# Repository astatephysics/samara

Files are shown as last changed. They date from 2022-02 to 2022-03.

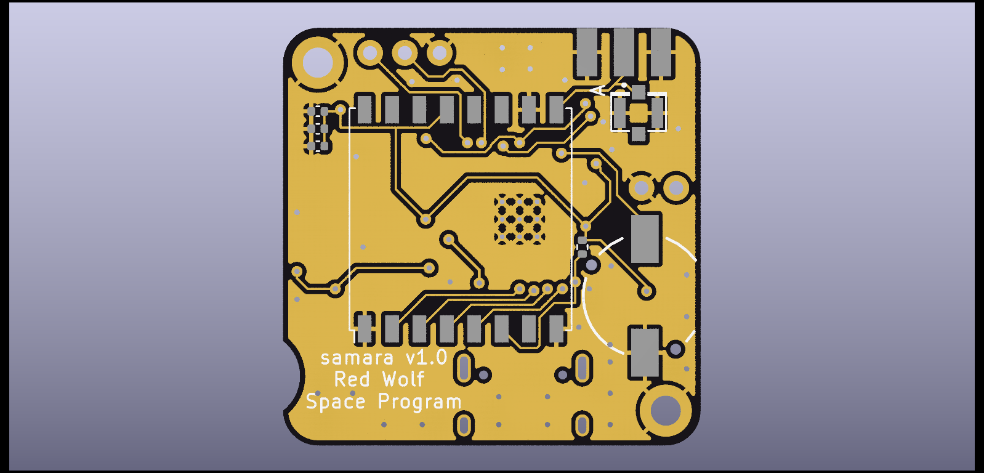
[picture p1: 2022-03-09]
samara-render-back.png

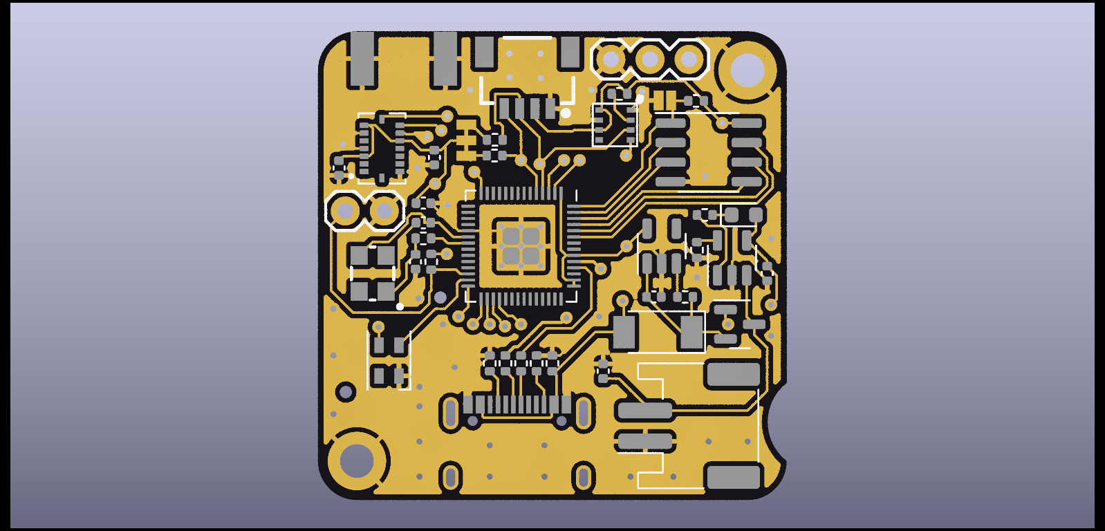
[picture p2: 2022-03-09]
samara-render-front.png

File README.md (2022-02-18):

# samara
Red Wolf Space Program's samara-style glider payload

----------------------------------------------------------
## Overview

Samara are a fruit with a fibrous wing-like structure that increases their wind-borne dispersal distances. Some of these like maple and ash seeds may slow their descent by autorotation as such they provide much entertainment for us humans who find them about. This project seeks to develop an airborne payload that mimic this behavior with a 3d printed airframe housing a radio antenna and this printed circuit board. 

This version of the board is contstrained to a 30.5mm x 30.5mm board and is inspired by "CricketSATs." This consists of a RP2040 microcontroller, BME280 temperature/humidity/pressure sensor, BNO055 inertial measurement unit, and RF95 LoRA radio. Several indicator leds are included as well as a surface mounted piezo buzzer. A STEMMA/Qwiic-compatable JST connector provides access to peripheral boards over I2C (e.g., GPS breakout board, realtime clocks, science payloads.)

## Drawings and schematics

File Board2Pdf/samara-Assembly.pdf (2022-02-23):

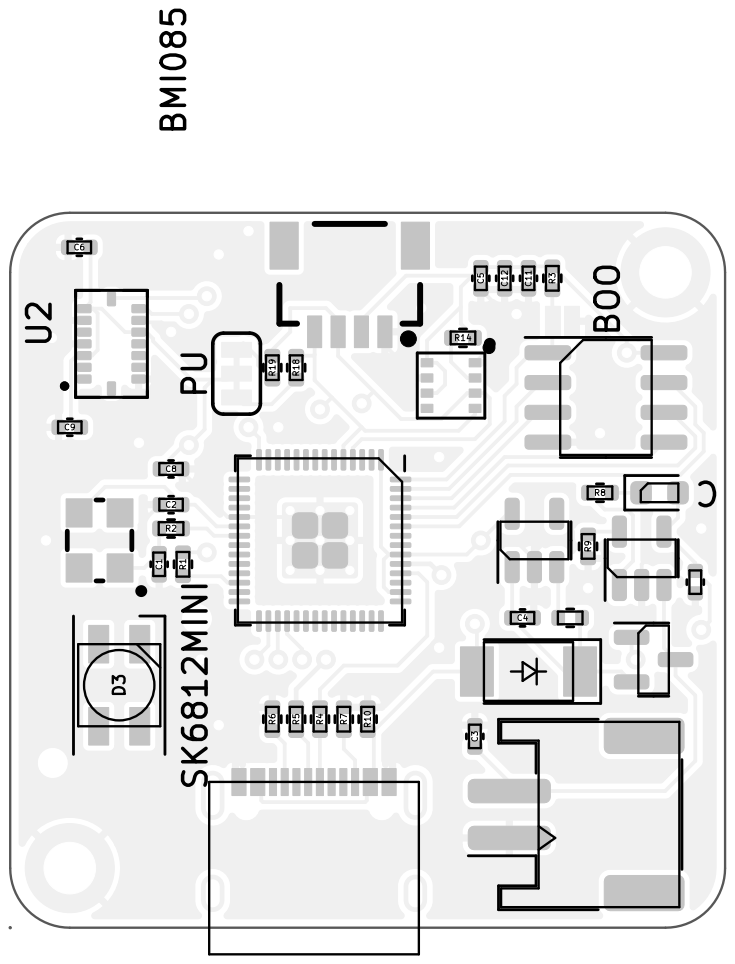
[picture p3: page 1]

Sheet: Assembly
File: samara.kicad_pcb
Id: 1/1 Title: samara payload prototype

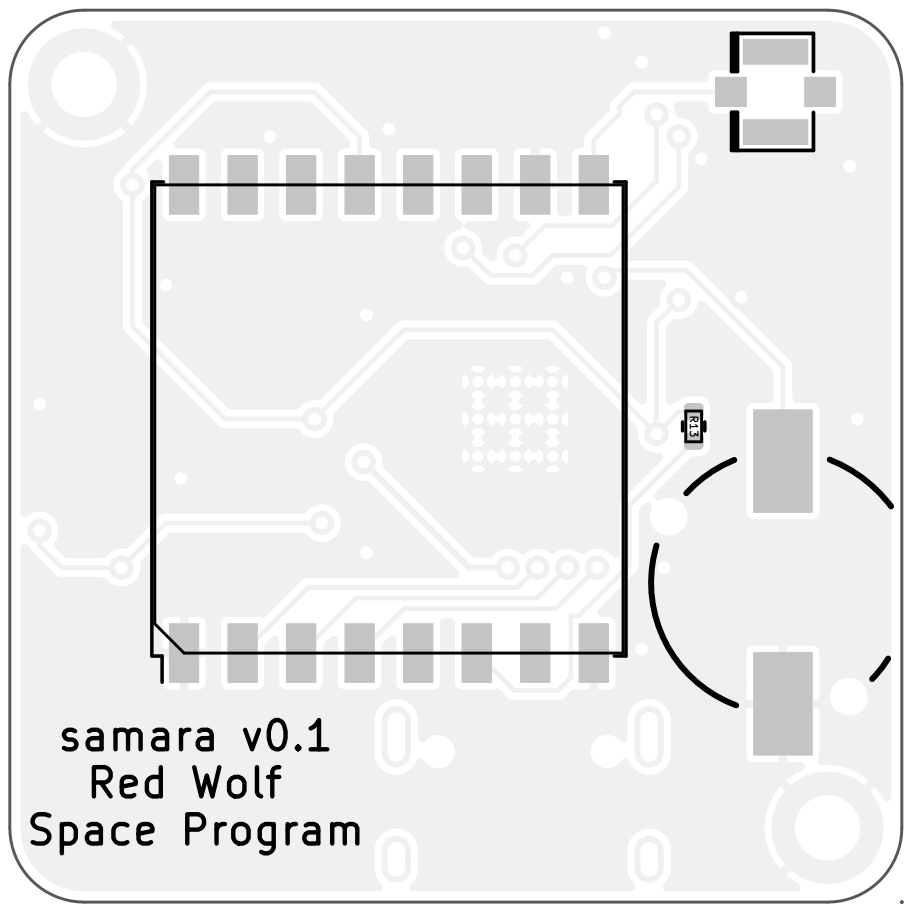
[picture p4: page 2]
D Date: KiCad E.D.A. kicad (6.0.1) Size: USLetter; Rev:

Arkansas State University R13

samara v0.1 Red Wolf Space Program

Sheet: Assembly
File: samara.kicad_pcb
Id: 1/1 Title: samara payload prototype

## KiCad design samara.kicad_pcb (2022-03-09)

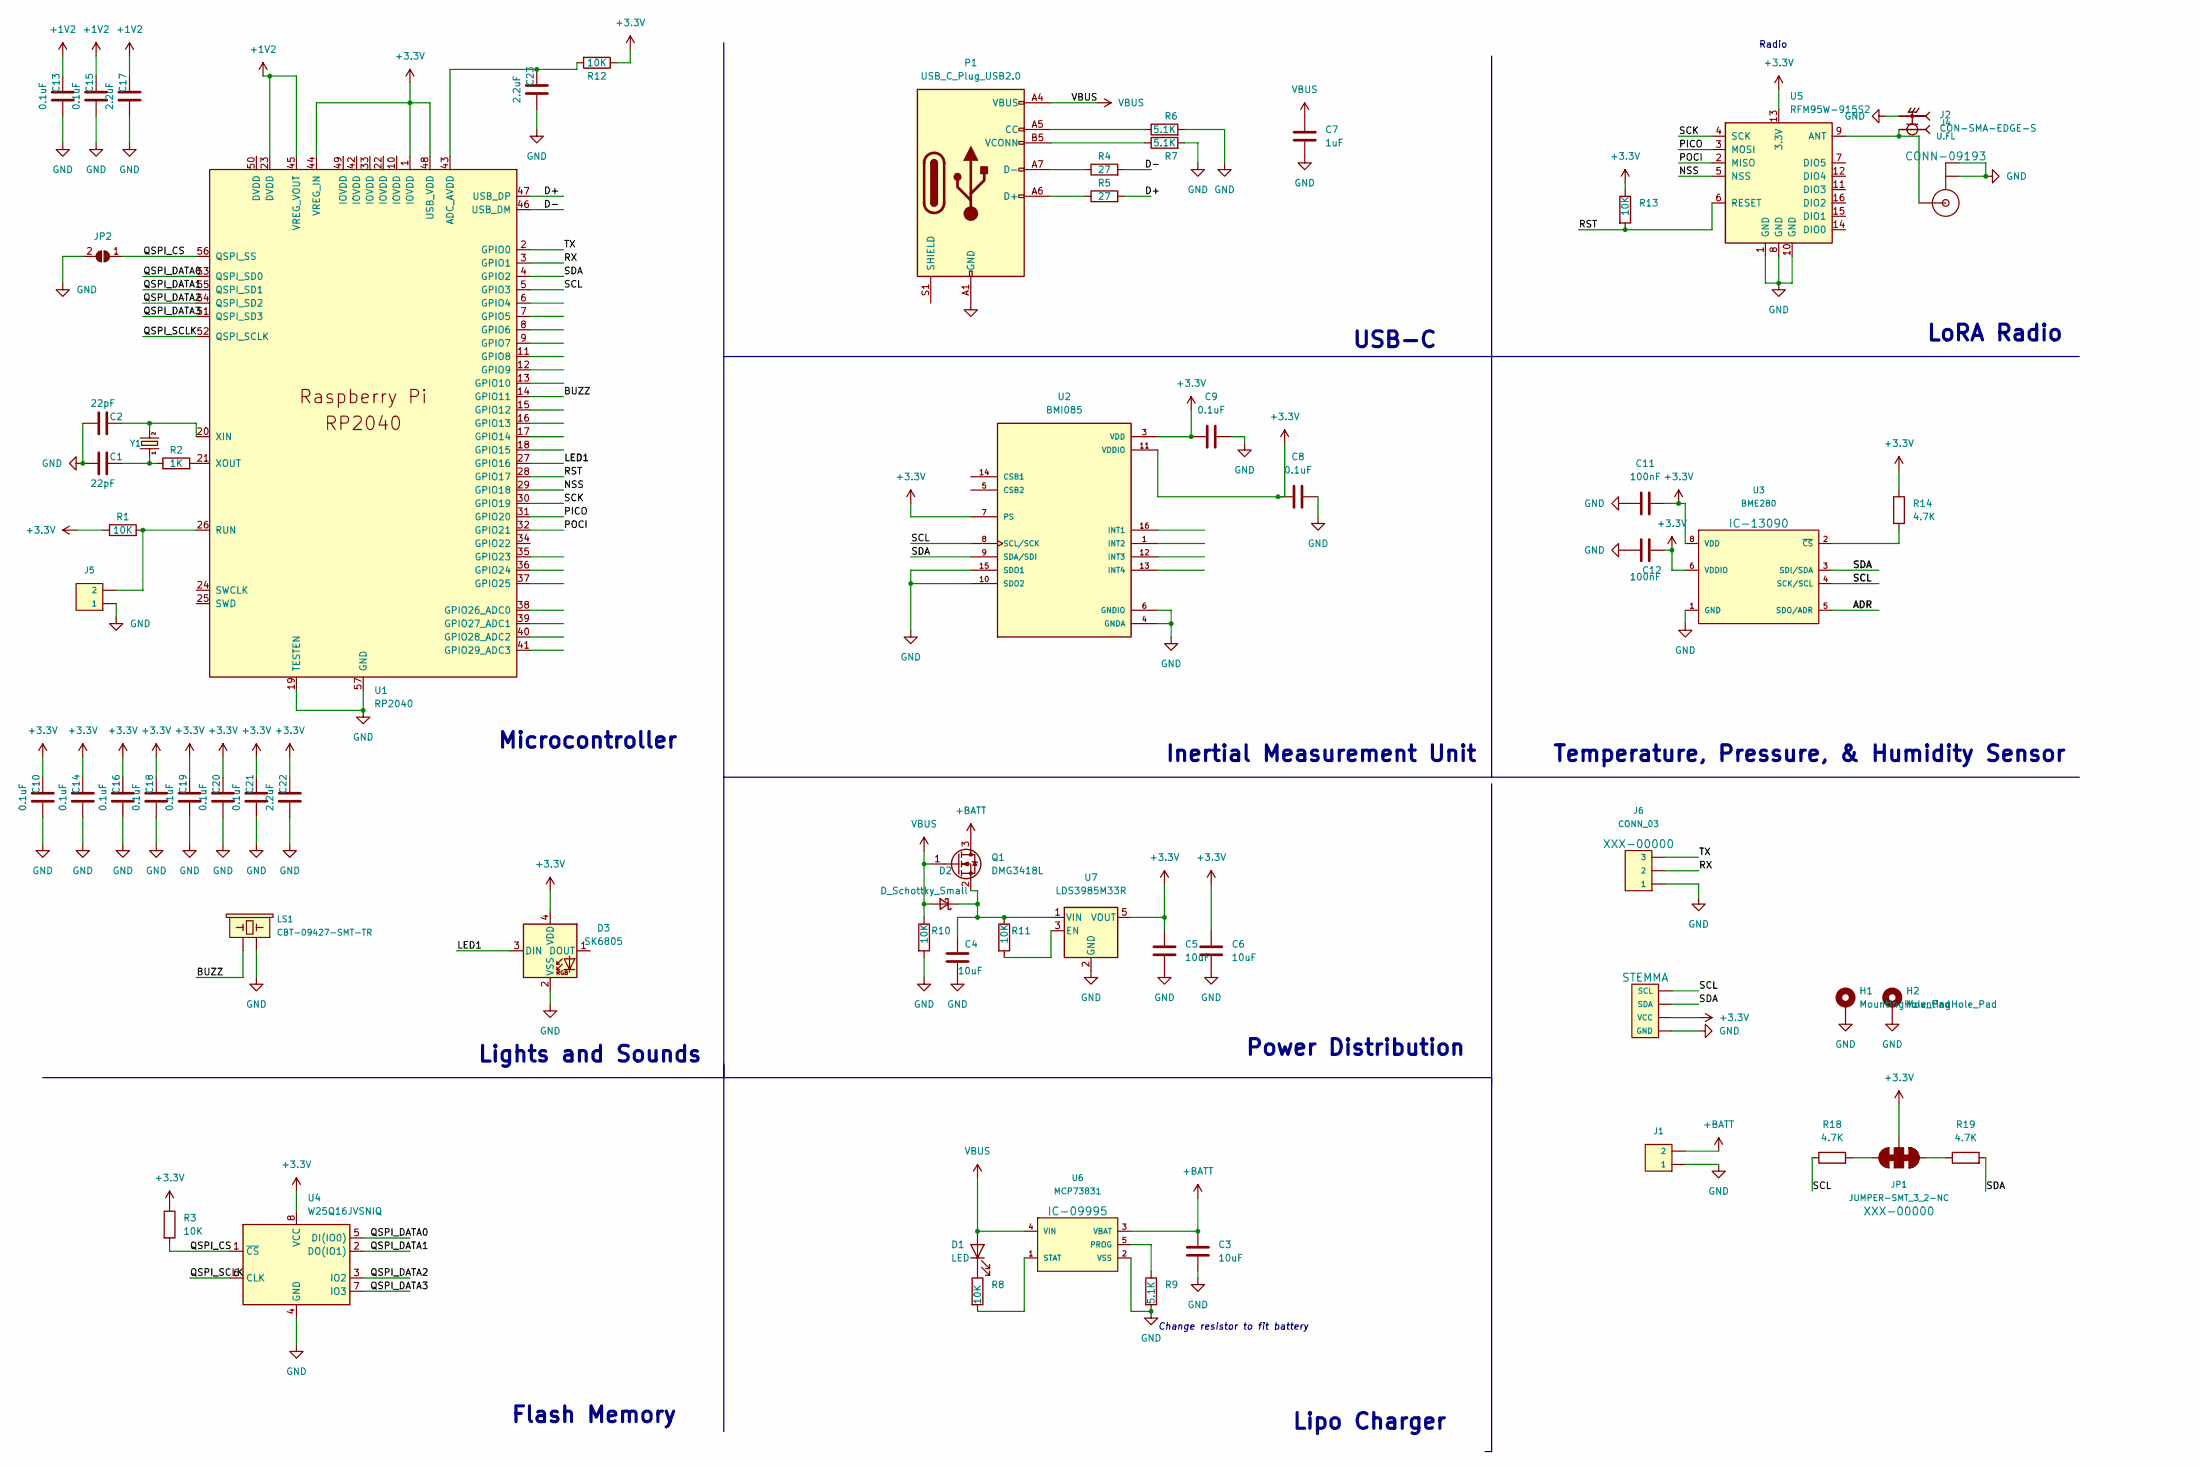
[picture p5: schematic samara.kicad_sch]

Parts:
C1, C2: 22pF; C_0402_1005Metric
C3, C4, C5, C6: 10uF; C_0402_1005Metric
C7: 1uF; C_0402_1005Metric
C8, C9, C10, C13, C14, C15, C16, C18, C19, C20, C21: 0.1uF; C_0402_1005Metric
C11, C12: 100nF; C_0402_1005Metric
C17, C22, C23: 2.2uF; C_0402_1005Metric
D1: LED; LED_0603_1608Metric
D2: D_Schottky_Small; D_SOD-128
D3: SK6805; LED_SK6805_PLCC4_2.4x2.7mm_P1.3mm
H1, H2: MountingHole_Pad; MountingHole_2.2mm_M2_DIN965_Pad_TopBottom
J1: CONN_02JST-PTH-2; JST_PH_S2B-PH-SM4-TB_1x02-1MP_P2.00mm_Horizontal
J2: CON-SMA-EDGE-S; RFSOLUTIONS_CON-SMA-EDGE-S; PARTREV 1
J3: I2C_STANDARDQWIIC; 1X04_1MM_RA
J4: U.FL
J5: CONN_02; 1X02
J6: CONN_03; 1X03
JP1: JUMPER-SMT_3_2-NC; SMT-JUMPER_3_2-NC_TRACE_SILK
JP2: SolderJumper_2_Open; SMT-JUMPER_2_NO_NO-SILK
LS1: CBT-09427-SMT-TR; BUZZER-CCV-KIT
P1: USB_C_Plug_USB2.0; USB_C_Receptacle_XKB_U262-16XN-4BVC11
Q1: DMG3418L; SOT-23
R1, R3, R8, R10, R11, R12, R13: 10K; R_0402_1005Metric
R2: 1K; R_0402_1005Metric
R4, R5: 27; R_0402_1005Metric
R6, R7, R9: 5.1K; R_0402_1005Metric
R14, R18, R19: 4.7K; R_0402_1005Metric
U1: RP2040; RP2040-QFN-56
U2: BMI085; PQFN50P450X300X100-16N; PARTREV 1.4
U3: BME280; LGA-8-2.5X2.5
U4: W25Q16JVSNIQ; SOIC-8_3.9x4.9mm_P1.27mm
U5: RFM95W-915S2; HOPERF_RFM9XW_SMD
U6: MCP73831; SOT-23-5
U7: LDS3985M33R; SOT-23-5
Y1: CRYSTAL-12MHZ"; CRYSTAL-SMD-3.2X2.5MM

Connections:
+1V2: C13.2, C15.2, C17.2, U1.23 (DVDD), U1.45 (VREG_VOUT)
+3V3: C5.1, C6.1, C8.1, C9.1, C10.2, C11.2, C12.2, C14.2, C16.2, C18.2, C19.2, C20.2, C21.2, C22.2, D3.4 (VDD), J3.2 (VCC), JP1.2, R1.1, R3.1, R12.1, R13.1, R14.1, U1.1 (IOVDD), U1.44 (VREG_IN), U1.48 (USB_VDD), U2.3 (VDD), U2.7 (PS), U2.11 (VDDIO), U3.6 (VDDIO), U3.8 (VDD), U4.8 (VCC), U5.13 (3.3V), U7.5 (VOUT)
+BATT: C3.1, J1.2, Q1.3 (D), U6.3 (VBAT)
/ADR: U3.5 (SDO/ADR)
/BUZZ: LS1.+ (1), U1.14 (GPIO11)
/D+: R5.2, U1.47 (USB_DP)
/D-: R4.2, U1.46 (USB_DM)
/LED1: D3.3 (DIN), U1.27 (GPIO16)
/NSS: U1.29 (GPIO18), U5.5 (NSS)
/PICO: U1.31 (GPIO20), U5.3 (MOSI)
/POCI: U1.32 (GPIO21), U5.2 (MISO)
/QSPI_CS: JP2.1 (A), R3.2, U1.56 (QSPI_SS), U4.1 (~CS)
/QSPI_DATA0: U1.53 (QSPI_SD0), U4.5 (DI(IO0))
/QSPI_DATA1: U1.55 (QSPI_SD1), U4.2 (DO(IO1))
/QSPI_DATA2: U1.54 (QSPI_SD2), U4.3 (IO2)
/QSPI_DATA3: U1.51 (QSPI_SD3), U4.7 (IO3)
/QSPI_SCLK: U1.52 (QSPI_SCLK), U4.6 (CLK)
/RST: R13.2, U1.28 (GPIO17), U5.6 (RESET)
/RX: J6.2, U1.3 (GPIO1)
/SCK: U1.30 (GPIO19), U5.4 (SCK)
/SCL: J3.4 (SCL), R18.1, U1.5 (GPIO3), U2.8 (SCL/SCK), U3.4 (SCK/SCL)
/SDA: J3.3 (SDA), R19.2, U1.4 (GPIO2), U2.9 (SDA/SDI), U3.3 (SDI/SDA)
/TX: J6.3, U1.2 (GPIO0)
GND: C1.1, C2.1, C3.2, C4.2, C5.2, C6.2, C7.2, C8.2, C9.2, C10.1, C11.1, C12.1, C13.1, C14.1, C15.1, C16.1, C17.1, C18.1, C19.1, C20.1, C21.1, C22.1, C23.1, D3.2 (VSS), H1.1, H2.1, J1.1, J2.G1, J2.G2, J2.G3, J2.G4, J3.1 (GND), J4.1 (GND), J4.2 (GND), J5.1, J6.1, JP2.2 (B), LS1.- (2), P1.A1 (GND), P1.A12 (GND), P1.B1 (GND), P1.B12 (GND), R6.2, R7.2, R9.2, R10.2, U1.19 (TESTEN), U1.57 (GND), U2.4 (GNDA), U2.6 (GNDIO), U2.10 (SDO2), U2.15 (SDO1), U3.1 (GND), U3.7 (GND), U4.4 (GND), U5.1 (GND), U5.8 (GND), U5.10 (GND), U6.2 (VSS), U7.2 (GND)
unnamed: C1.2, R2.1, Y1.1
unnamed: C2.2, U1.20 (XIN), Y1.3 (2)
unnamed: C4.1, D2.1 (K), Q1.2 (S), R11.1, U7.1 (VIN)
unnamed: D1.1 (K), R8.1
unnamed: J2.1, J4.FEED (SIGNAL), U5.9 (ANT)
unnamed: J5.2, R1.2, U1.26 (RUN)
unnamed: JP1.1, R19.1
unnamed: JP1.3, R18.2
unnamed: P1.A5 (CC), R6.1
unnamed: P1.A6 (D+), R5.1
unnamed: P1.A7 (D-), R4.1
unnamed: P1.B5 (VCONN), R7.1
unnamed: R2.2, U1.21 (XOUT)
unnamed: R8.2, U6.1 (STAT)
unnamed: R9.1, U6.5 (PROG)
unnamed: R11.2, U7.3 (EN)
unnamed: R14.2, U3.2 (~CS)
unnamed: C23.2, R12.2, U1.43 (ADC_AVDD)
VBUS: C7.1, D1.2 (A), D2.2 (A), P1.A4 (VBUS), P1.A9 (VBUS), P1.B4 (VBUS), P1.B9 (VBUS), Q1.1 (G), R10.1, U6.4 (VIN)

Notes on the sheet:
Radio
Microcontroller
Flash Memory
Power Distribution
Inertial Measurement Unit
Lipo Charger
LoRA Radio
Lights and Sounds
USB-C
Temperature, Pressure, & Humidity Sensor
Change resistor to fit battery

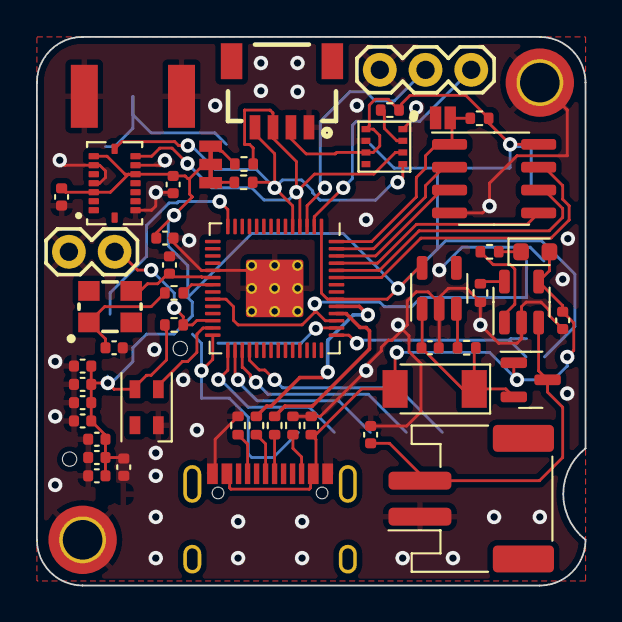
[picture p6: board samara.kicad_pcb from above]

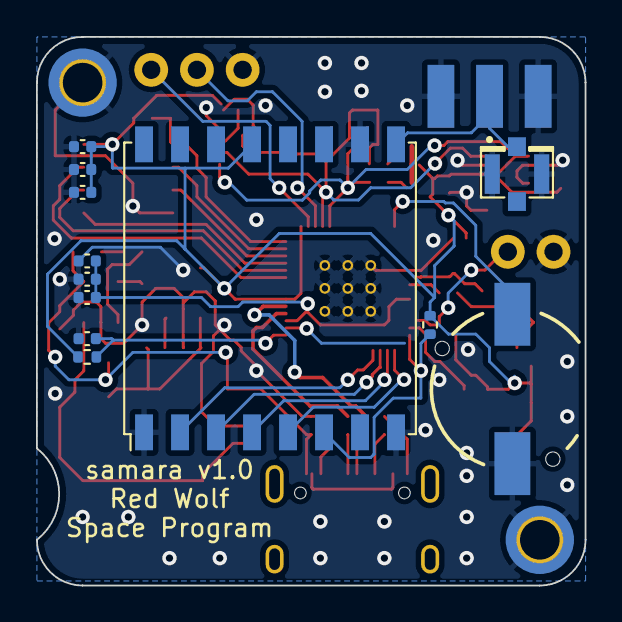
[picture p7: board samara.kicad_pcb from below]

Board: 2 copper layers, 30.5 x 30.5 mm, 63 parts (13 on the bottom side), 42 nets.

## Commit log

2022-02-18 initial pcb layout
    [samara.kicad_pcb, samara.kicad_sch]
2022-02-22 updated IMU to BMI085
    [samara.kicad_pcb, samara.kicad_sch]
2022-02-23 update 3d models
    [samara.kicad_pcb, samara.kicad_sch]
2022-03-03 assorted updates and 3d models
    [samara.kicad_pcb, samara.kicad_sch]
2022-03-07 close to v1 production
    [samara-B_Cu.gbl, samara-B_Mask.gbs, samara-B_Paste.gbp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]
2022-03-09 ready for first pcb fab
    get ready for bodges...
    [samara.kicad_pcb, samara.kicad_sch]
